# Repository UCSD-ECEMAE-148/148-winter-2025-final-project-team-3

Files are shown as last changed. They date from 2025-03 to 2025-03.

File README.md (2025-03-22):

# <div align="center">Autonomous Stock Relief</div>

### <div align="center"> MAE 148 Final Project </div>
#### <div align="center"> Team 3 Winter 2025 </div>
<p align = center>
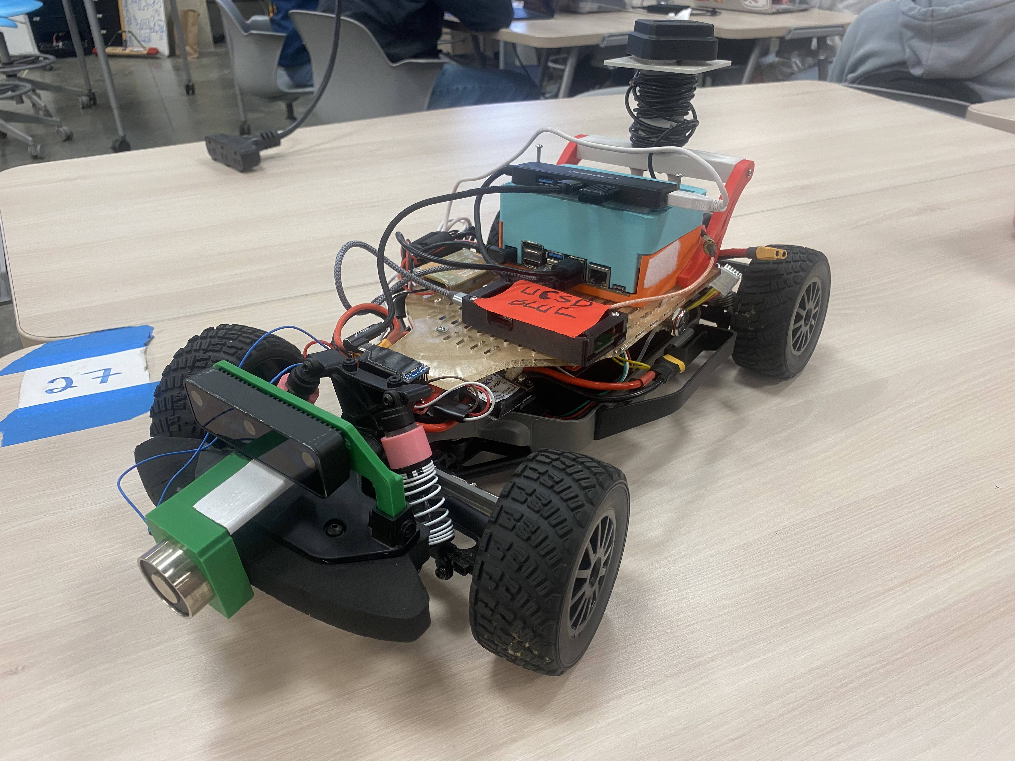
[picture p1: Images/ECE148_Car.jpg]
  
</p>

## Table of Contents
  <ol>
    <li><a href="#team-members">Team Members</a></li>
    <li><a href="#abstract">Abstract</a></li>
    <li><a href="#what-we-promised">Promises and Stretch Goals</a></li>
    <li><a href="#accomplishments">Accomplishments</a></li>
    <li><a href="#challenges">Challenges</a></li>
    <li><a href="#Potential-Improvements">Potential Improvements</a></li>
    <li><a href="#Demonstrations">Demonstrations</a></li>
    <li><a href="#Robot-Design">Robot Design</a></li>
      <ul>
        <li><a href="#Mechanical-Designs">Mechanical Designs</a></li>
        <li><a href="#Electrical-System-Diagram">Electrical System Diagram</a></li>
      </ul>
  </ol>
<hr>

## Team Members
Anton John Del Mar - ECE ML & Controls - Class of 2025

Tigran Grigoryan - MAE Controls & Robotics - Class of 2027

Kanishk Mehta - MAE Aerospace - Class of 2026

Juan Sanchez - MAE Aerospace Flight Dynamics and Control- Class of 2026
<hr>

## Abstract
The goal of our project was to create a bot that would be able to navigate between different warehouses and transport supply from overflowing warehouses to one's with less stock. To navigate between the warehouses the idea was the employ GNSS and once inside the warehouse, the bot would utilize a model running on the OAK-D Lite in order to identify boxes and pick them up with a grabbing mechanism in order to transport.
<hr>

## Promises and Stretch Goals
Promised
* Integrate GNSS, OAK-D model, and Grabber Mechanism into the ROS2 system.

Stretch Goals
* Create a "A*" algorithm in order to find the shortest distance between two warehouses and take that route.
* Integrate lidar into ROS2 system in an effort for obstacle avoidance, following a global path until reaching an obstacle and using lidar to follow a local path avoiding the obstacle and getting back onto the global path.
<hr>

## Accomplishments
- Created and integrated custom electromagnet grabber mechanism.
- Developed April Tag detection algorithm for autonomous loading of supplies.
  - Integrated our own custom PID control to self-align towards boxes with April Tags.
- Created custom GPS algorithm for autonomous navigation to warehouse points.
  - Also used custom PID control along with cross track error algorithm to stay on path.
  - Used .csv files and parsed them for GPS coordinates
<hr>

## Challenges
- Our electronics mount broke during the race, causing us to have to redesign a base and reintegrate our electronics.
- We initially made our own electromagnet, however could not integrate it with the relay circuit, causing us to have to use a store bought one.
- The first camera mount we created was too high and since it was adujustable the angle could change and require us to recallibrate our April Tag detection. We thus created a new short, fixed camera mount that also could hold our electromagnet.
- It took one week to debug and get our GPS to work. We tried two different repositories for the PointOneNav, tried different Docker containers, tried uninstalling and reinstalling the fusion-engine-driver, we tried other GPS modules, we even tried to use the Ublox, all to no avail. After one week of trieless debugging and suffering, it turns out it really was just our module. Our module simply did not work with the fusion-engine-driver in ROS2, but our TA Winston had a module that did and he let us use his.
- A lot of restless coding, debugging, and testing, trying to integrate our autonomous system fully in ROS2. 
- Issues with our Docker container caused us to lose some code and have to rewrite it.
- Jetson SD card was corrupted the day before our final presentation, and we could not save our Docker conatiner. Causing us to have to reflash our SD card, reinstall and setup everything such as pulling and setting up the Docker image, and also having to rewrite a lot of missing code.
- Created our own topic and message interface for our GPS and April Tag nodes, but then our VESC stopped working, preventing us from testing the interface.

<hr>

## Potential Improvements
- Create a new camera mount such that the camera is a bit farther back, because since the camera was in the front it could not see the April Tag if it was too close.
- Design a different electromagnet grabber, our design required the boxes to be on a little pallet. Maybe have the electromagnet pick up boxes from above like a crane.
- Integrate a better circuit design using perf boards or even a PCB rather than just connecting everything with wires and electrical tape. 
- Complete testing the custom topic and interface to fully integrate the April Tag and GPS nodes. 

<hr>

## Progress Videos

### Electromagnet Testing
**Description:**  
Demonstration of our custom electromagnet, and later the Arduino relay circuit with a store bought electromagnet communicating via SPI to the Jetson.

Custom Electromagnet (https://youtube.com/shorts/Nj_8vAmQDf4?feature=share)
Jetson and Arduino Talking (https://youtube.com/shorts/6ehe19gdT4E?feature=share)

### April Tag Testing
**Description:**  
Initial April Tag detection algorithm, April Tag detection without PID tuning, and finally April Tag detection with PID tuning as well as a POV shot of what the robot sees during self-alignment.

Inital April Tag Detection (https://youtube.com/shorts/lWoA0QRKPfw?feature=share)
No PID (https://youtube.com/shorts/V5mrUUOpYhs?feature=share)
April Tag PID (https://youtube.com/shorts/OQ9bbp3Mwuc?feature=share)
April Tag PID POV (https://youtube.com/shorts/0pPFK0INl1c?feature=share)

### GPS Testing
**Description:**  
Initial GPS testing without PID tuning.

GPS no PID (https://youtube.com/shorts/9fqmz0wuvG4?feature=share)

<hr>

## Final Demonstrations

### April Tag Detection and GPS Navigation
**Description:**  
Sucessfull autonomous loading of supply with April Tag Detection using PID tuning. Succesfull autonomous navigation to a warehouse point 'A' using GPS and PID tuning as well.

Final April Tag (https://youtube.com/shorts/S16Okz2q1UY?feature=share)
Final GPS (https://youtube.com/shorts/vWnwtKYyrfo?feature=share)

<hr>

## Robot Design

### Mechanical Designs
| Part | CAD Model |
|---|---|
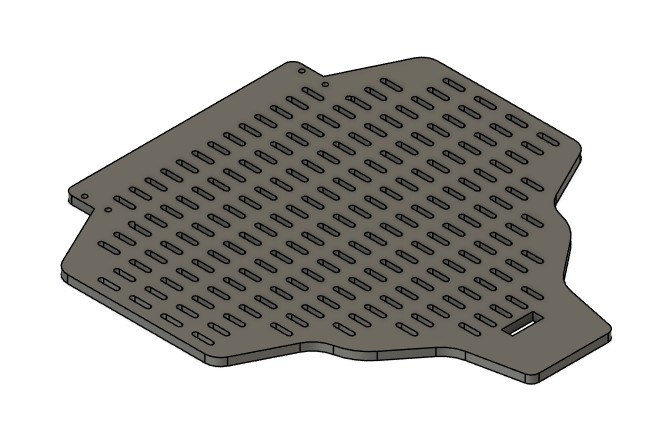
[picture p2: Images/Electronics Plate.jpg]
Electronics Plate
| Electronics Mounting Plate | <br>[🔗 CAD File](CAD%20Files/New%20Chassis/Electronics%20plate%20v13.f3d) |
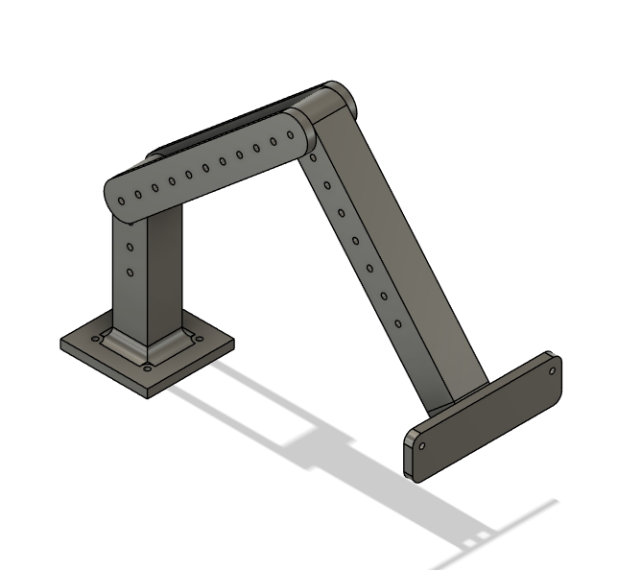
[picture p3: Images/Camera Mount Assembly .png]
Camera Mount
| Camera Mount | <br>[🔗 CAD File](CAD%20Files/New%20Chassis/Camera%20Mount/Camera%20Mount%20assembly%20v5.f3z) |
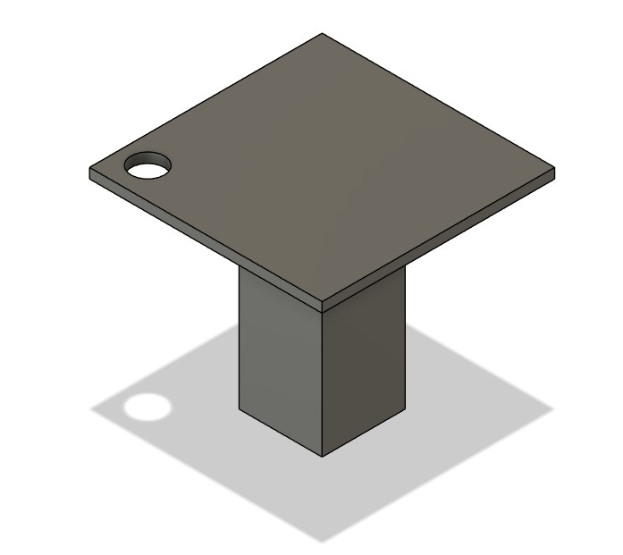
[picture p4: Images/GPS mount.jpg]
GPS Mount
| GPS Mount | <br>[🔗 CAD File](CAD%20Files/New%20Chassis/Gps%20mount%20v2.f3d) |
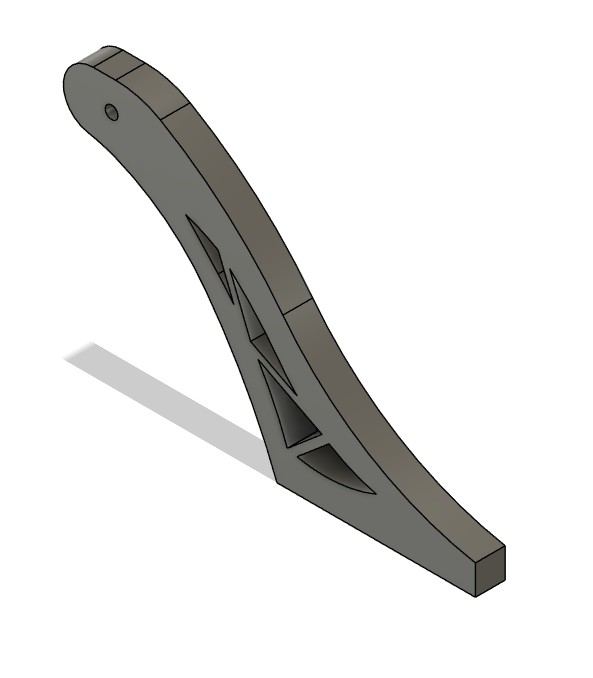
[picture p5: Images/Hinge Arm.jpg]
Hinge Arm
| Hinge Arm | <br>[🔗 CAD File](CAD%20Files/New%20Chassis/Hinge%20arm%20v8.f3d) |
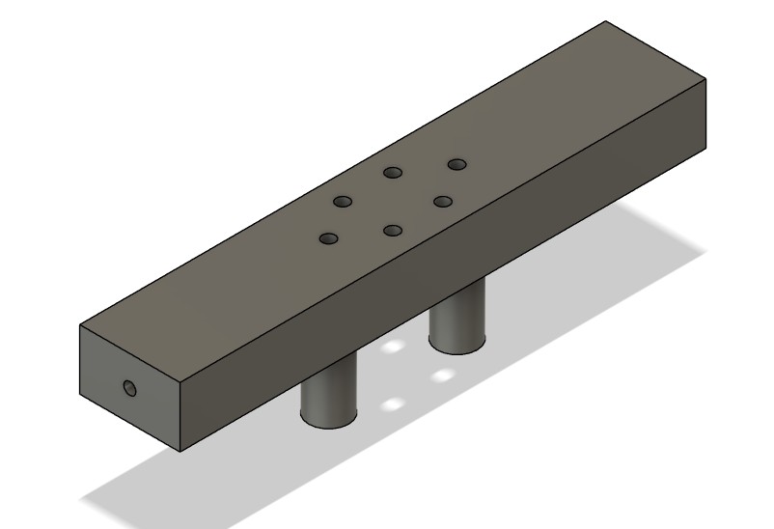
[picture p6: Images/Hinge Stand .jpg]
Hinge and GPS stand
| Hinge and GPS stand | <br>[🔗 CAD File](CAD%20Files/New%20Chassis/GPS+hinge%20stand%20v8.f3d) |
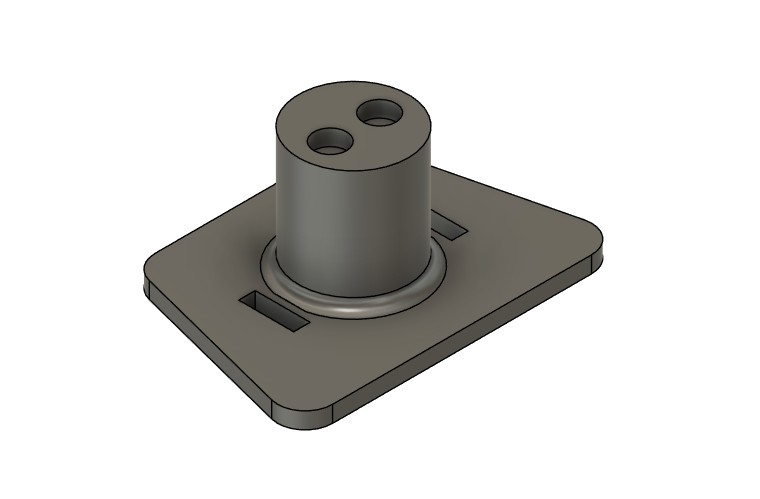
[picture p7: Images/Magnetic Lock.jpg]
Magnetic Lock
| Magnetic Lock | <br>[🔗 CAD File](CAD%20Files/New%20Chassis/Magnetic%20Lock%20v7.f3d) |
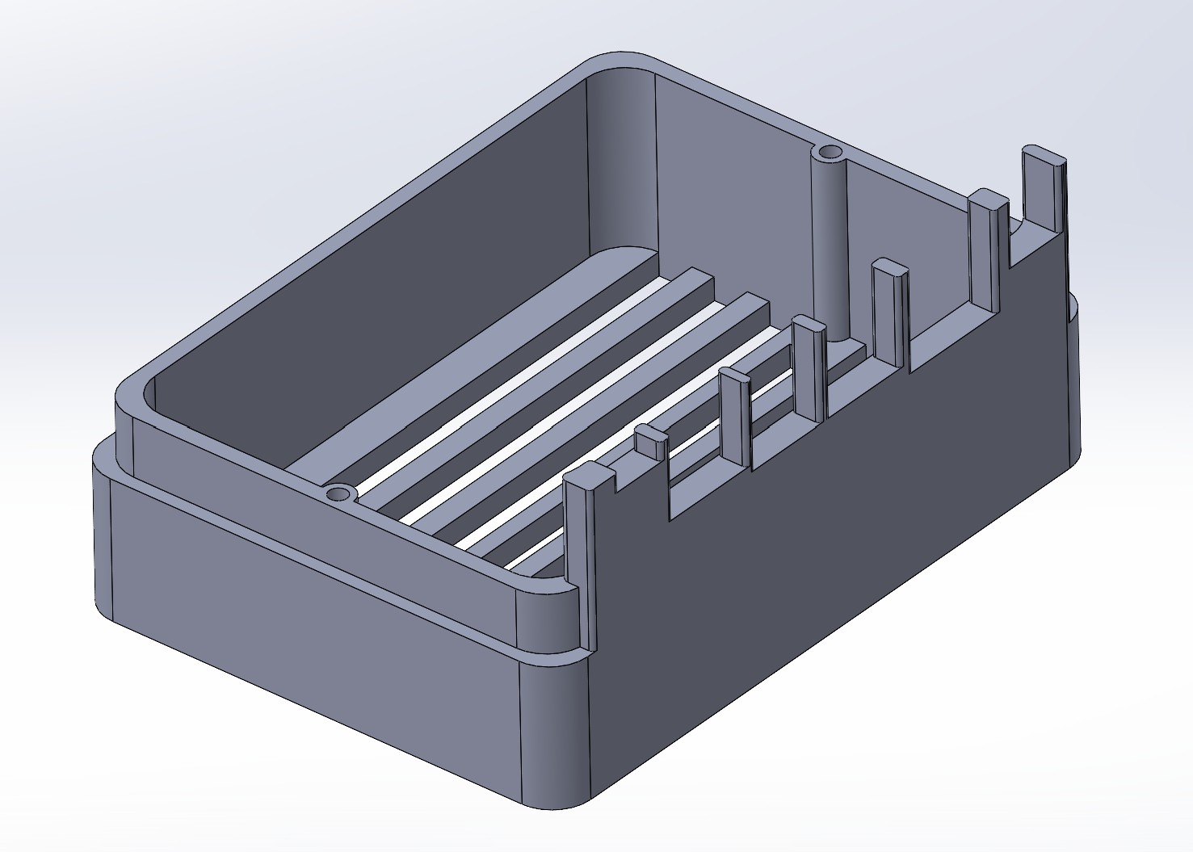
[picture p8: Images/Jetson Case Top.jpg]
Jetson Case
| Jetson Case Top | <br>[🔗 CAD File](CAD%20Files/New%20Chassis/Jetson%20Top%20V1.SLDPRT) |
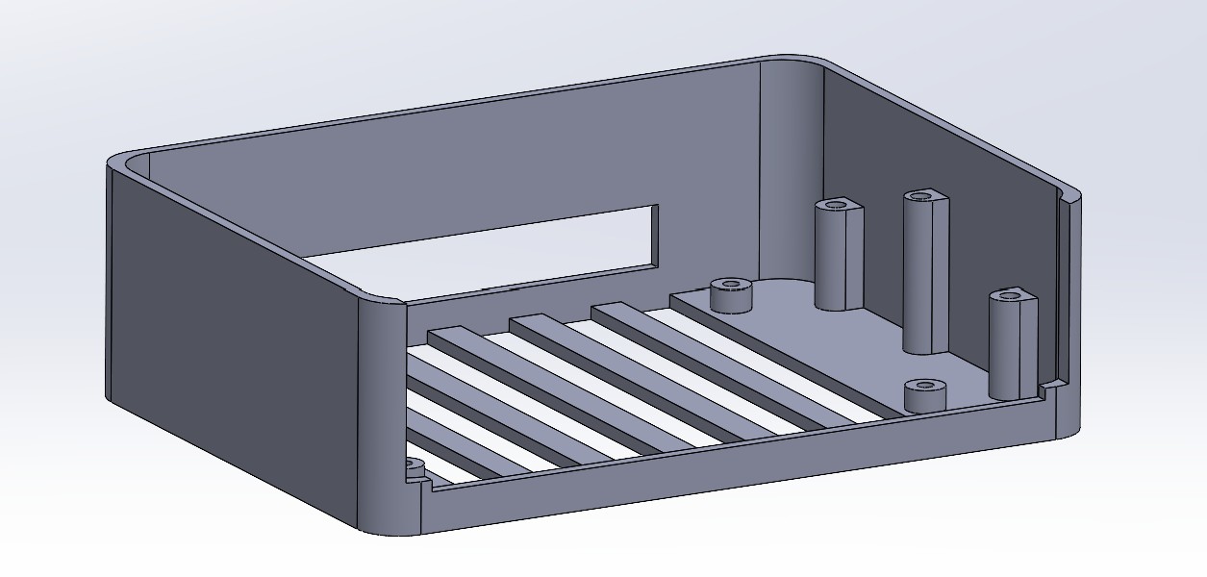
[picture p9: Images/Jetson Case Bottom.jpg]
Jetson Case
| Jetson Case Bottom | <br>[🔗 CAD File](CAD%20Files/New%20Chassis/Jetson%20Bottom%20V1.SLDPRT) |
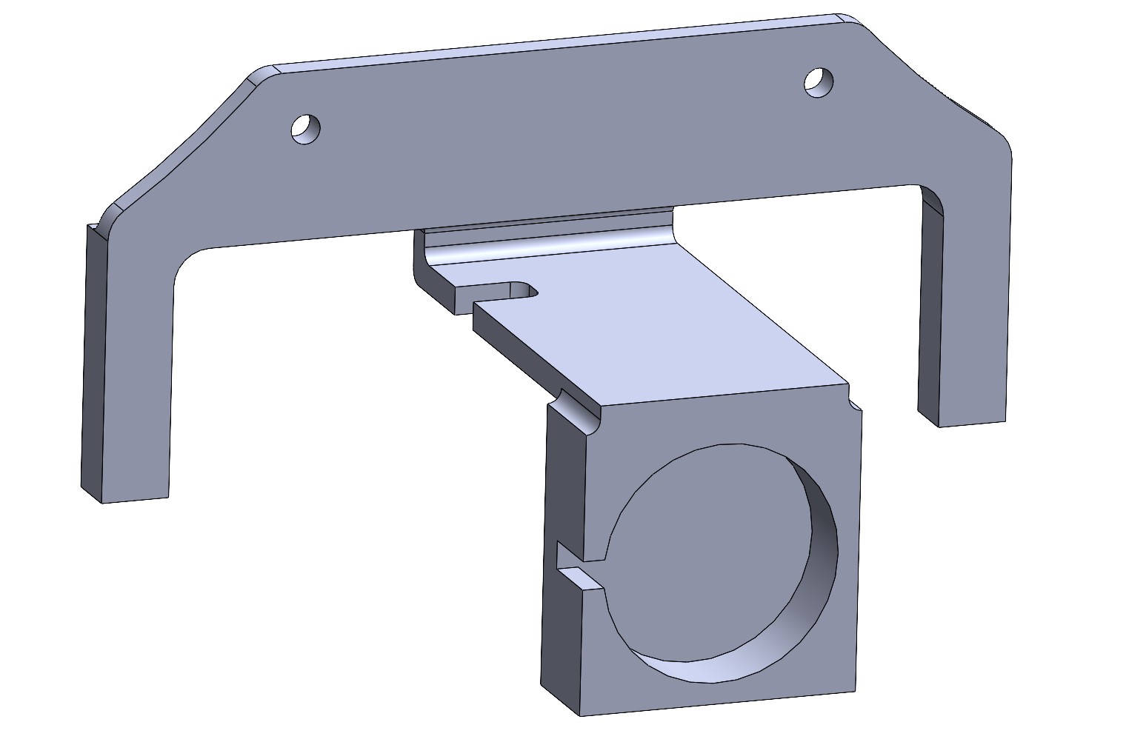
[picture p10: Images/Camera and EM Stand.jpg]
| Camera and ElectroMagnet Stand | <br>[🔗 CAD File](CAD%20Files/New%20Chassis/Camera%20and%20EM%20Stand.SLDPRT) |
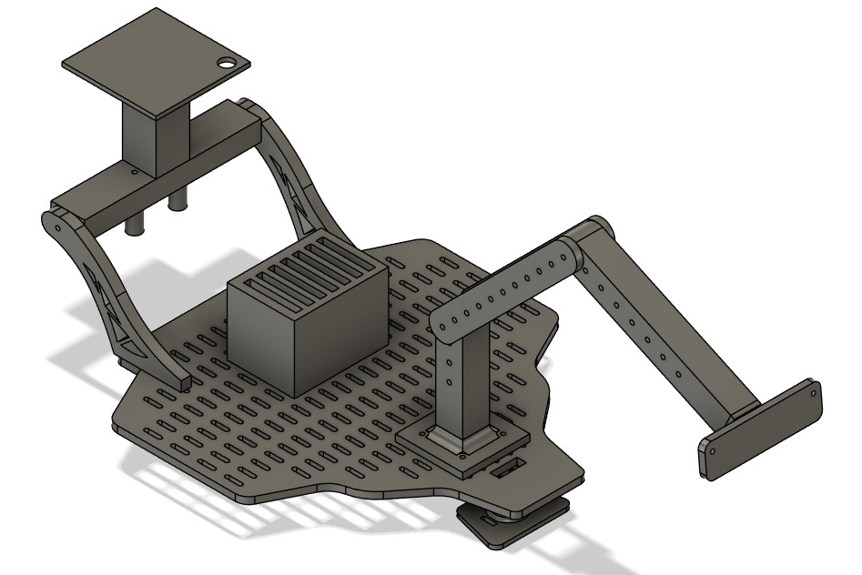
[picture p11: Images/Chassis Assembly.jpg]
New Chassis Assembly
| New Chassis Assembly | <br>[🔗 CAD File](CAD%20Files/New%20Chassis/Assemply%20v7.f3z) |

<hr>

### Electrical System Diagram
| Comprehensive Wiring Diagram |
|------|
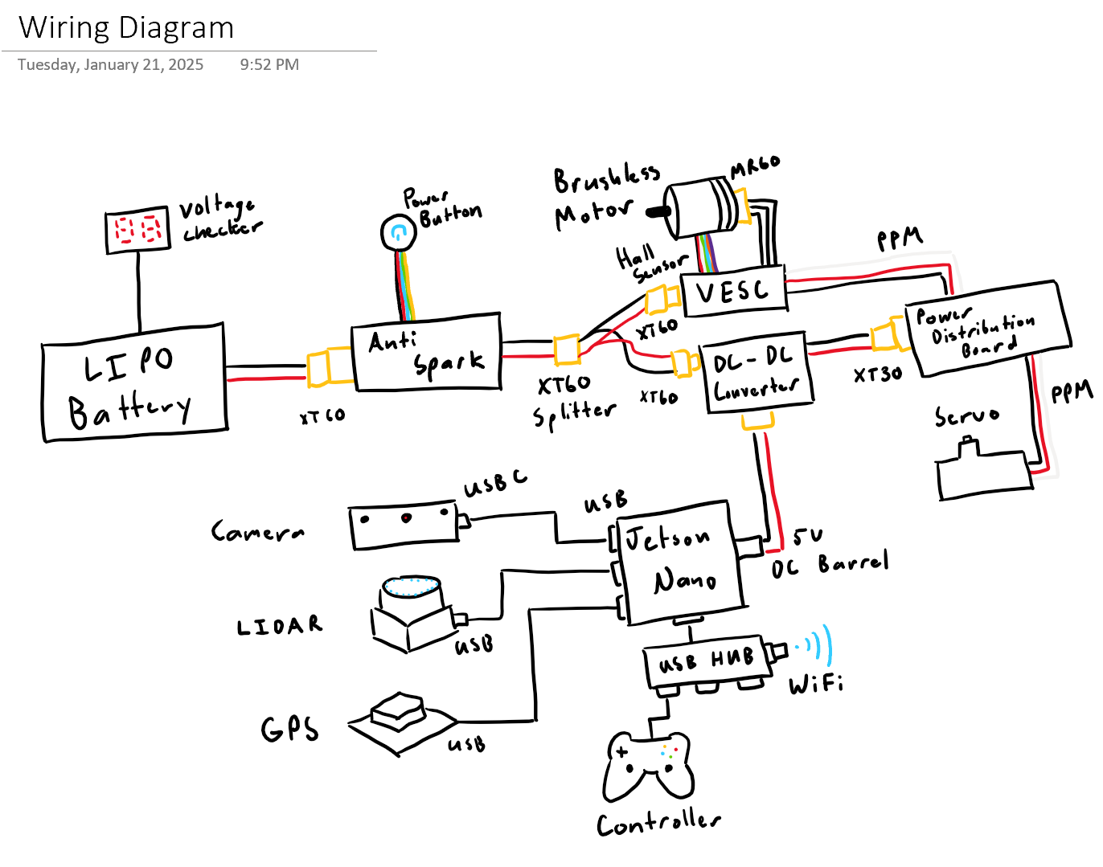
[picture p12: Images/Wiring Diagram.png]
Comprehensive Wiring Diagram
|  |

<hr>

## Software Design 
### Overview 
Our project was completed using ROS2 through the djnighti/ucsd_robocar container, also utilizing libraries such as DepthAI AprilTag and pymap3d. With the use of ROS2 we were able to have free reign over our code allowing for full control and custom development of our autonomous system.

### Code Explanations 
april_tag_detector.py, car_control.py, PID.py
- april_tag_detector.py: We succesfully utilized ROS2 and DepthAI's April Tag library in order to allow our OAK-D camera to detect April Tags. We calculate how far the April Tag is and how off-center it is as well to determine how much to turn and drive.
  - Created a custom circuit that used an Arduino Pro Micro to control a relay to turn on and off our electromagnet, then used Python's serial library to allow our Jetson to interface with the circuit and turn on the electromagnet when needed. 
- car_control.py: we use the /drive topic with ackermann_msgs/msg/AckermannDriveStamped interface message type to control speed and steering angle of the bot.
- PID.py: With initial testing we found our robot would turn too much in proportion to the error. We created a PID class to help fine tune our robots self-alignment with April Tags.

gps_navigation.py, coordinates.csv
- gps_navigation.py: We succesfully utilized the PointOneNav GNSS in ROS2 order to get global positions and navigate between warehouses. Using Python's pymap3d library we can convert global coordinates into relative coordinates. For navigation we use pandas library to read a .csv file tellings us the origin and the coordinate of a warehouse, then simply use y = mx + b to determine the path by creating a straight line to the warehouse. We can now use cross track error and the determinant of two vectors to see how we deviate from the line and see which side we are on, and then use our PID class to realign ourselves onto the path.
- coordinates.csv: Holds the coordinates for the warehouse and origin.

final_project.launch.py, gps_april_msgs
- final_project.launch.py: Created a launch file that would launch our april_tag_detector.py and gps_navigation.py nodes, as well as the ucsd_robocar_nav2_pkg all_nodes.launch.py that would launch the vesc node.
- gps_april_msgs: Created a custom message interface called gps_april_msgs/msg/GpsApril along with a new topic named /GpsApril to allow the April Tag and GPS nodes to talk to eachother. This interface contained important information like if the robot was in approach mode or origin mode to tell it if it needs to drive to a warehouse or return to an origin, the warehouse name it needs to go to, as well as GPS mode and April Tag mode to well it when to run April Tag detection or GPS navigation.

### Implementation
If you wish to implement our code into your own project it is really simple! You can use the same container as you did for the OpenCV laps as we used the djnighti image with ROS2 for this one. All of our code was completed inside the ucsd_robocar_nav2_pkg, so simply add the code into this package. Make sure you add the executables in setup.py and if you rename them make sure to modify the launch file as well. If you want to create your own topic or interface you have to create a new package in ucsd_robocar_hub2, where all the packages are stored, in this case you can simply copy our folder as it has set up all the Cmake files already, you simply would just have to change the names to whatever you want. That is about it, have fun and goodluck!

<hr>

## Gantt Chart
<p align = center>
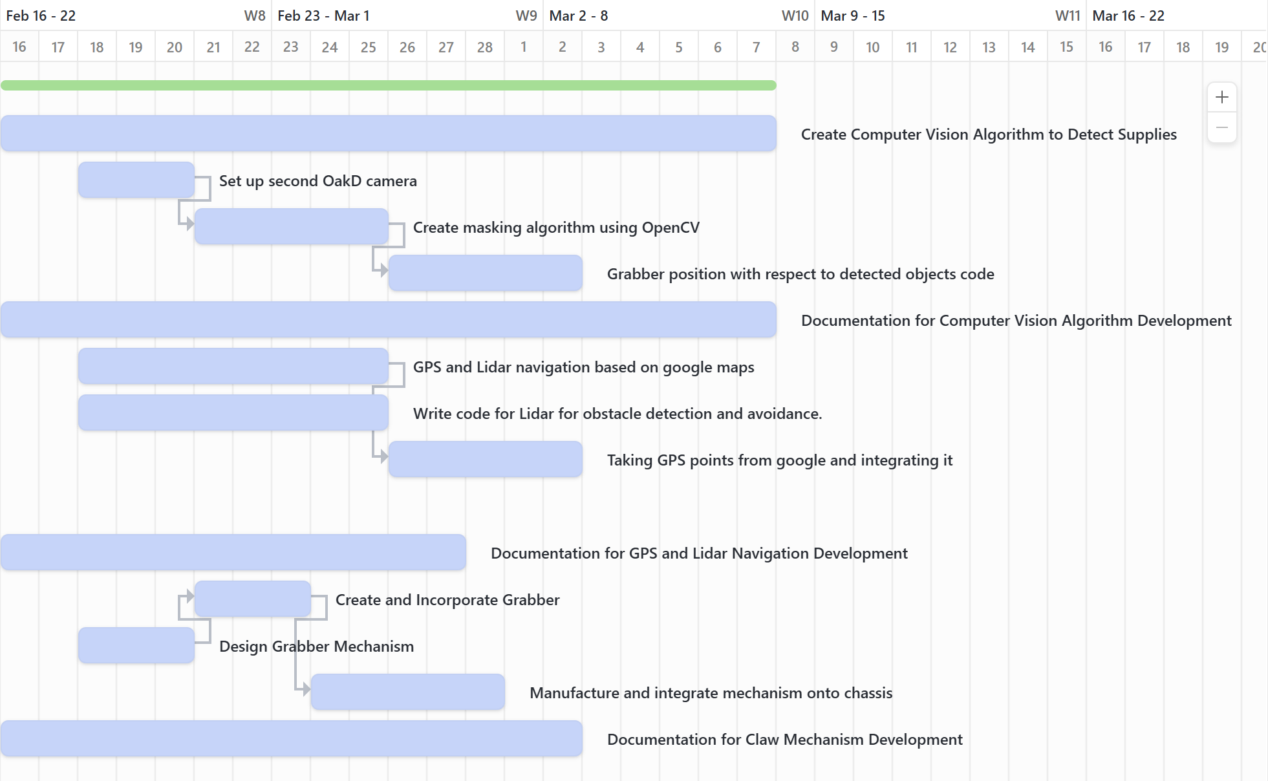
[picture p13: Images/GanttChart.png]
  
</p>

<hr>

## Course Deliverables
Here are all the team assignments we had to complete for the course.
- [Autonomous Laps](https://youtube.com/shorts/bM4KuNR4FdE?si=LPRqq_h8zV2o7q9d)
- [GPS Laps](https://youtu.be/LaXMkxYxspk)
- [OpenCV Laps](https://youtu.be/_cmjnNDHkDQ?si=lZVS0dAk0vt-fLF-)
- [Progress Update Slides](https://docs.google.com/presentation/d/1vnkvjQhTCcCYGIWP700G1c7TLgcMM7nZI48wmxLYrfw/edit?usp=sharing)
- [Final Presentation Slides](https://docs.google.com/presentation/d/1t6mhh3AGAhgKwmr5gQEw1CEoPPurwSvcvcnYaqPXGoU/edit?usp=sharing)

<hr>

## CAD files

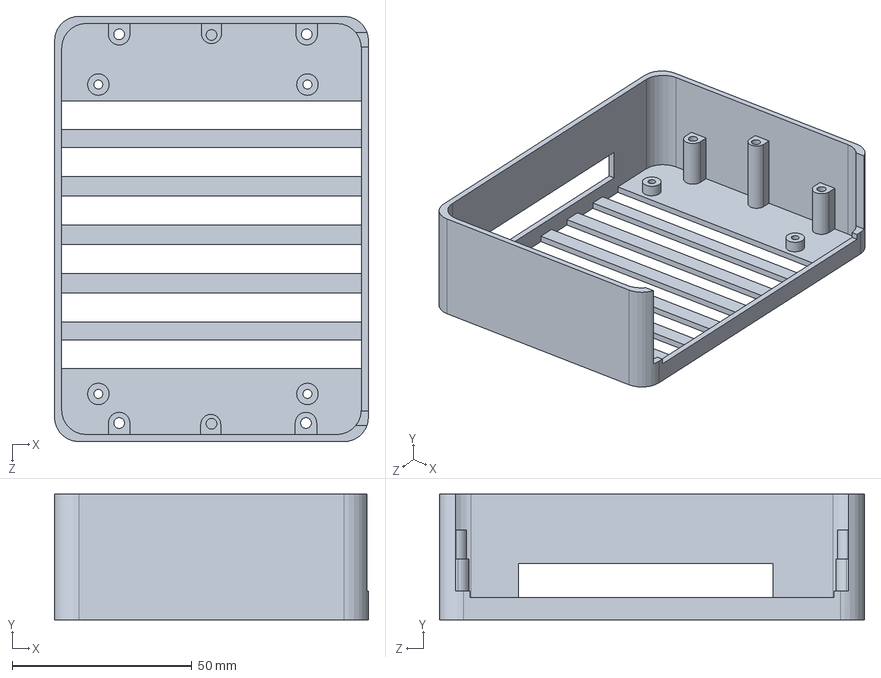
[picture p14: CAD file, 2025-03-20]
CAD Files/New Chassis/Jetson Bottom V1.SLDPRT
87.4 x 35.0 x 118.4 mm

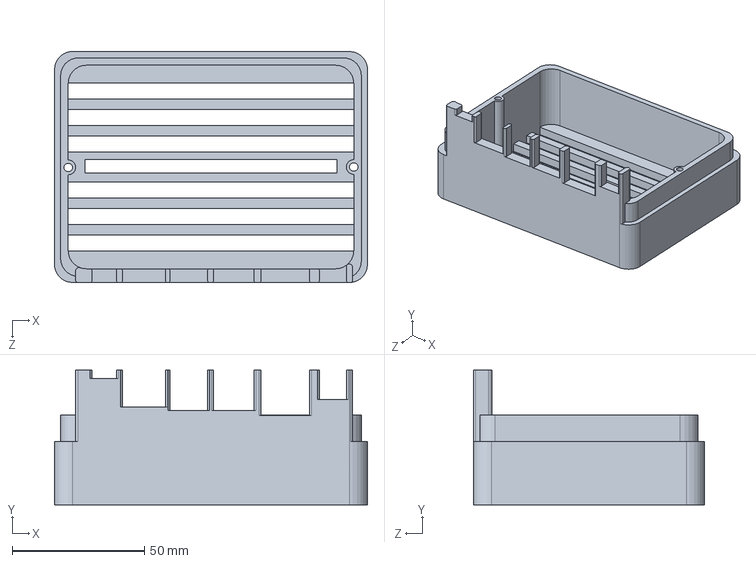
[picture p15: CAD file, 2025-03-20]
CAD Files/New Chassis/Jetson Top V1.SLDPRT
118.4 x 51.0 x 87.4 mm

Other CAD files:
CAD Files/New Chassis/Assemply v7.f3z
CAD Files/New Chassis/Camera Mount/Camera Mount assembly v5.f3z
CAD Files/New Chassis/Camera Mount/Camera arm 1 v5.f3d
CAD Files/New Chassis/Camera Mount/Camera arm 2 v4.f3d
CAD Files/New Chassis/Camera Mount/Camera mount negative v2.f3d
CAD Files/New Chassis/Camera Mount/Camera mount v2.f3d
CAD Files/New Chassis/Camera Mount/camera stand v4.f3d
CAD Files/New Chassis/Electronics plate v13.f3d
CAD Files/New Chassis/GPS+hinge stand v8.f3d
CAD Files/New Chassis/Gps mount v2.f3d
CAD Files/New Chassis/Hinge arm v8.f3d
CAD Files/New Chassis/Magnetic Lock v7.f3d
CAD Files/Old Chassis/Old_Camera Mount v1.f3d
CAD Files/Old Chassis/Old_Electronics plate v1.f3d
CAD Files/Old Chassis/Old_gps mount v2.f3d

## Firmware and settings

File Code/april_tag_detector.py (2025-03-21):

import cv2
import depthai as dai
import numpy as np
import serial
import time
from numpy import interp

import rclpy
from rclpy.node import Node

from ucsd_robocar_nav2_pkg.car_control import moveCar
from ucsd_robocar_nav2_pkg.PID import controlPID

from gps_april_msgs.msg import GpsApril


class AprilTag(Node):
	def __init__(self):
		super().__init__("april_tag_node"); 
		self.declare_parameter('detect', False); 
		self.declare_parameter('visualize', False); 
		
		self.checkDetect = self.get_parameter('detect').value; 
		self.checkVisualize = self.get_parameter('detect').value; 
		
		self.talkPublisher = self.create_publisher(GpsApril, '/talkGpsApril', 10); 
		self.talkSubscriber = self.create_subscription(
			GpsApril,
			'/talkGpsApril',
			self.GpsAprilChecker,
			10
		); 
		self.talkSubscriber; 
		
		self.theCar = moveCar(); 
		self.theCar.stopCar(); 
		self.PID = controlPID(Kp = 0.4, Ki = 0, Kd = 0.15, theError = 0.0); 
		
		self.targetID = 0; 
		self.theThreshold = 12000; # Box is about 6in away
		
		self.theSerial = serial.Serial(port = "/dev/ttyACM0", baudrate = 9600); 
		
		self.aprilMode = False; 
	
		if self.checkDetect: 
			self.aprilDetection(); 
			
	def GpsAprilChecker(self, theMessage):
		self.get_logger().info("Message Received: " + str(theMessage)); 
		self.aprilMode = theMessage.april_mode; 
	
	
	def aprilDetection(self): 
		thePipeline = dai.Pipeline(); 
		cameraRGB = thePipeline.create(dai.node.ColorCamera); 
		# print(str(cameraRGB.getResolution())); 
		cameraRGB.setPreviewSize(960, 540); # Our camera is 1080, so 1920 x 1080 frame size
		cameraRGB.setInterleaved(False); 
		cameraRGB.setFps(30); 
		
		aprilTag = thePipeline.create(dai.node.AprilTag); 
		cameraRGB.video.link(aprilTag.inputImage); 
		
		xOutDetections = thePipeline.create(dai.node.XLinkOut); 
		xOutDetections.setStreamName("Detection Stream"); 
		aprilTag.out.link(xOutDetections.input); 
		
		xOutVideo = thePipeline.create(dai.node.XLinkOut); 
		xOutVideo.setStreamName("Video Stream"); 
		cameraRGB.preview.link(xOutVideo.input); 
			
		with dai.Device(thePipeline) as theDevice:
			aprilQueue = theDevice.getOutputQueue(name = "Detection Stream", maxSize = 4, blocking = False);
			videoQueue = theDevice.getOutputQueue(name = "Video Stream", maxSize = 4, blocking = False);
		
			while True: 
				if self.aprilMode:
					try:
						theDetections = aprilQueue.get(); 
					except RuntimeError as theError:
						self.get_logger().info("Camera Error: " + str(theError));
						time.sleep(4); 
						continue; 
							
					theFrame = videoQueue.get().getCvFrame(); 
					
					if self.checkVisualize: 
						cv2.line(theFrame, (480, 540), (480, 0), (0, 255, 0), 2); 
				
					if theDetections is not None: 
						for aDetection in theDetections.aprilTags:
							tagID = aDetection.id; 
							# self.get_logger().info("Tag ID: " + str(tagID));  
							# Map coordinate to our preview size using interpolate
							xBR = aDetection.bottomRight.x; 
							xBR = int(np.interp(xBR, [0, 1920], [0, 960])); 
							yBR = aDetection.bottomRight.y; 
							yBR = int(np.interp(yBR, [0, 1080], [0, 540])); 
							# self.get_logger().info("Bottom Right Coordinate: " + str(xBR) + ", " + str(yBR)); 
							
							xTL = aDetection.topLeft.x; 
							xTL = int(np.interp(xTL, [0, 1920], [0, 960])); 
							yTL = aDetection.topLeft.y; 
							yTL = int(np.interp(yTL, [0, 1080], [0, 540])); 
							# self.get_logger().info("Top Left Coordinate: " + str(xTL) + ", " + str(yTL)); 
							
							xMiddle = int(xBR - ((xBR - xTL)/2)); 
							yMiddle = int(yTL - ((yTL - yBR)/2)); 
								
							theError = xMiddle - 480; 
							self.get_logger().info("Error: " + str(theError)); 
							
							theHeight = int(yTL - yBR); 
							theWidth = int(xBR - xTL); 
							
							theArea = np.abs(theHeight * theWidth); 
							self.get_logger().info("Area: " + str(theArea)); 
						
							if tagID == self.targetID:
								if theArea < self.theThreshold:
									theAngle = self.PID.computePID(theError); 
									theAngle = np.interp(theAngle, [-180, 180], [-0.5, 0.5]); 
									self.get_logger().info("Angle: " + str(theAngle)); 
									self.theCar.driveCar(0.3, theAngle); 
									time.sleep(1); 
									
								if theArea > self.theThreshold:
									self.theSerial.write("on".encode('Ascii')); 
									time.sleep(1); 
								
									theAngle = self.PID.computePID(theError); 
									theAngle = np.interp(theAngle, [-180, 180], [-0.5, 0.5]); 
									self.get_logger().info("Angle: " + str(theAngle)); 
									self.theCar.driveCar(0.4, theAngle); 
									time.sleep(2); 
									self.theCar.driveCar(-0.3, 0.0); 
									
									self.theCar.turnAround(); 
									self.theCar.driveCar(0.5, 0.0); 
									self.theSerial.write("off".encode('Ascii')); 
									self.theSerial.close(); 
									time.sleep(2); 
									self.theCar.driveCar(-0.5, 0.0); 
								
							if self.checkVisualize:
								cv2.rectangle(theFrame, (xTL, yTL), (xBR, yBR), (255, 0, 0), 2); 
								cv2.line(theFrame, (xMiddle, yMiddle), (480, yMiddle), (0, 0, 255), 2); 
								cv2.putText(theFrame, str(tagID), (xMiddle, yMiddle), cv2.FONT_HERSHEY_SIMPLEX, 1, (255, 255, 255), 2, cv2.LINE_AA); 
							 				
					 
					if self.checkVisualize:
						cv2.imshow("April Tag", theFrame); 
					
					if cv2.waitKey(1) and 0xFF == ord('q'):
						break; 
						
				cv2.destroyAllWindows(); 
				 
				 

def main(args = None): 
	rclpy.init(args = args); 
	
	nodeAprilTag = AprilTag(); 
	
	rclpy.spin(nodeAprilTag); 
	
	rclpy.shutdown(); 
	
	
	
if __name__ == '__main__':
	main(); 

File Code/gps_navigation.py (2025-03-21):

import os
import pandas as pd
import numpy as np
import pymap3d as pmap

import rclpy
from rclpy.node import Node
from rclpy.qos import QoSProfile, ReliabilityPolicy, DurabilityPolicy

from sensor_msgs.msg import NavSatFix
from ucsd_robocar_nav2_pkg.car_control import moveCar
from ucsd_robocar_nav2_pkg.PID import controlPID

from gps_april_msgs.msg import GpsApril


class gpsNavigationNode(Node):
	def __init__(self):
		super().__init__("gps_navigation_node"); 
		# self.get_logger().info("GPS Node Activated!");

		# self.get_logger().info(str(os.getcwd()));
		dataFrame = pd.read_csv("src/ucsd_robocar_hub2/ucsd_robocar_nav2_pkg/ucsd_robocar_nav2_pkg/coordinates.csv");

		# theData = self.parseData(dataFrame);

		# self.get_logger().info(str(theData['A']));

		theQoS = QoSProfile(depth = 10, reliability=ReliabilityPolicy.BEST_EFFORT, durability=DurabilityPolicy.VOLATILE);
		self.theSubscriber = self.create_subscription(
			NavSatFix,
			'/fix',
			self.getCoordinate,
			theQoS
		); 
		self.theSubscriber; 
		
		self.talkPublisher = self.create_publisher(GpsApril, '/talkGpsApril', 10);
		self.talkSubscriber = self.create_subscription(
			GpsApril,
			'/talkGpsApril',
			self.GpsAprilChecker,
			10
		); 
		self.talkSubscriber; 


		self.theLat0 = 32.88115036131583; 
		self.theLon0 = -117.23339932288448; 
		self.theAlt0 = 74.33511395566165; 

		csvInfo = self.parseData(dataFrame); 
		self.theTarget = csvInfo['A']; 
		self.theTargetE = self.theTarget[0]; 
		self.theTargetN = self.theTarget[1]; 
		
		# Initialize interface, we start with GPS
		theMessage = GpsApril(); 
		theMessage.target_name = "A"; 
		theMessage.approach_target = True; 
		theMessage.gps_mode = True; 
		self.talkPublisher.publish(theMessage); 
		
		self.PID = controlPID(Kp = 0.2, Ki = 0, Kd = 0.12, theError = 0.0); 
		self.theCar = moveCar(); 
		self.theCar.stopCar(); 
		
		self.approachTarget = False; 
		self.returnOrigin = False; 
		self.targetName = ""; 
		self.gpsMode = False; 
		
		
	def GpsAprilChecker(self, theMessage):
		self.get_logger().info("Message Received: " + str(theMessage)); 
		self.approachTarget = theMessage.approach_target; 
		self.returnOrigin = theMessage.return_origin; 
		self.targetName = theMessage.target_name; 
		self.gpsMode = theMessage.gps_mode; 
		
		
	def euclideanDistance(self, theE, theN, theU):
		theDistance = np.sqrt((self.theTargetE - theE)**2 + (self.theTargetN - theN)**2);
		return theDistance; 


	def lineSide(self, theE, theN): # Which side of the line we are on using the determinant of two vectors
		# Determine the side of the line we are on using sign function
		# det = (x2 - x1)*(p_y - y1) - (y2 - y1)*(p_x - x1);
		# Origin = (x1, y1), Target = (x2, y2), Point = (p_x, p_y);
		# We want to check if the point is on the left or right of the line made by origin and target
		# If the determinant is greater than 0 it is left, less than it is right, exactly 0 is on line
		x1 = 0; y1 = 0; x2 = self.theTargetE; y2 = self.theTargetN; 
		p_x = theE; p_y = theN; 
		theDeterminant = (x2 - x1)*(p_y - y1) - (y2 - y1)*(p_x - x1); 
		return np.sign(theDeterminant); 
		
		
	def crossTrackError(self, theE, theN): # How far a point is from a line
		# Distance from line = Ax + By + C / sqrt(A**2 + B**2);
		# Ax + By + C = 0, y = mx + b, mx - y + b = 0, C = b, B = -1, A = m
		A = self.theTargetN/self.theTargetE; B = -1; C = 0; 
		x = theE; y = theN; 
		CTE = (np.abs(A*x + B*y + C) / np.sqrt(A**2 + B**2)); 
		return CTE; 
		
		
	def driveTarget(self, theE, theN, theU):
		# self.get_logger().info(str(self.gpsMode)); 
		if self.gpsMode and self.approachTarget:
			theDistance = self.euclideanDistance(theE, theN, theU); 
			self.get_logger().info("Euclidean Distance: " + str(theDistance)); 

			theCTE = self.crossTrackError(theE, theN); # Distance from line
			theCTE = theCTE*self.lineSide(theE, theN); # Side of line
			self.get_logger().info("Cross Track Error: " + str(theCTE)); 

			if theDistance < 0.7:
				self.theCar.stopCar(); 
				theMessage = GpsApril(); 
				theMessage.approach_target = False; 
				theMessage.gps_mode = False; 
				theMessage.april_mode = True; 
				self.talkPublisher.publish(theMessage); 

			else:
				theAngle = self.PID.computePID(theCTE); 
				self.get_logger().info("Angle: " + str(theAngle)); 
				self.theCar.continuousDrive(0.3, theAngle); 


	def getCoordinate(self, theMessage):
		NS = theMessage.latitude; # (+) = North, (-) = South
		EW = theMessage.longitude; # (+) = East, (-) = West
		ALT = theMessage.altitude; 
		self.get_logger().info(f"East: {EW}, North: {NS},  Alt: {ALT}"); 

		# Convert to ENU
		theE, theN, theU = pmap.geodetic2enu(NS, EW, ALT, self.theLat0, self.theLon0, self.theAlt0); 

		self.get_logger().info(f"E: {theE}, N: {theN}, U: {theU}"); 
		self.driveTarget(theE, theN, theU); 


	def parseData(self, dataFrame):
		dataDictionary = {}; 
		for anIndex, aRow in dataFrame.iterrows():
			# self.get_logger().info(f"Index: {anIndex}");
			# self.get_logger().info(f"Warehouse: {aRow['warehouse']}, East: {aRow['east']}, North: {aRow['north']}");
			dataDictionary.update({aRow['warehouse']: (aRow['east'], aRow['north'], aRow['up'])}); 
		return dataDictionary; 


def main(args = None):
	rclpy.init(args = args); 

	gpsNode = gpsNavigationNode(); 

	rclpy.spin(gpsNode); 

	gpsNode.destroy_node(); 
	rclpy.shutdown(); 


if __name__ == '__main__':
	main(); 

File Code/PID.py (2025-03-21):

import time


class controlPID():  
	def __init__(self, Kp, Ki, Kd, theError = 0): 
		self.previousError = theError; 
		self.previousTime = time.time(); 
		self.integralTerm = 0;  
		
		self.Kp = Kp; 
		self.Ki = Ki; 
		self.Kd = Kd; 
		
		
	def computePID(self, theError): 
		currentTime = time.time(); 
		errorDifference = theError - self.previousError; 
		timeDifference = currentTime - self.previousTime; 
		
		if timeDifference == 0: 
			timeDifference = 1; # Prevent division by 0 
		
		proportionalTerm = self.Kp * theError; 
		
		self.integralTerm += theError * timeDifference; 
		integralTerm = self.Ki *self.integralTerm; 
		
		derivativeTerm = errorDifference / timeDifference; 
		derivativeTerm = self.Kd * derivativeTerm; 
		
		PID = proportionalTerm + integralTerm + derivativeTerm; 
		
		self.previousError = theError; 
		self.previousTime = currentTime; 
		
		return PID; 

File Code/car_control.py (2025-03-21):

import numpy as np
import time
from rclpy.node import Node

from ackermann_msgs.msg import AckermannDriveStamped as ADS


class moveCar(Node): 
    def __init__(self):
    	super().__init__('move_car_node'); 
        self.thePublisher = self.create_publisher(ADS, '/drive', 10); 
        
    
    def driveCar(self, theSpeed, theAngle):
        theMessage = ADS(); 
        theMessage.drive.speed = theSpeed; 
        theMessage.drive.steering_angle = theAngle; 
        self.thePublisher.publish(theMessage); 
        time.sleep(0.5); 
        theMessage.drive.speed = 0.0; 
        self.thePublisher.publish(theMessage); 
        time.sleep(0.5); 
         
    
    def stopCar(self): 
        theMessage = ADS(); 
        theMessage.drive.speed = 0.0; 
        theMessage.drive.steering_angle = 0.0; 
        self.thePublisher.publish(theMessage); 
        time.sleep(0.5)
        
    
    def turnAround(self): 
	    self.driveCar(-0.8, 0.7); 
        self.driveCar(-0.8, 0.7); 
        self.driveCar(-0.8, 0.7); 
        time.sleep(1); 
        self.driveCar(0.8, -0.7); 
        self.driveCar(0.8, -0.7); 
        self.driveCar(0.8, -0.5); time.sleep(1); 
	    
	
    def continuousDrive(self, theSpeed, theAngle):
        theMessage = ADS(); 
        theMessage.drive.speed = theSpeed; 
        theMessage.drive.steering_angle = theAngle; 
        self.thePublisher.publish(theMessage);	    
        

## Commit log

2025-03-16 Create Old Chassis
    Old chassis files
2025-03-16 Delete CAD Files directory
    Remaking the thing
2025-03-16 Create New chassis files
2025-03-16 Delete CAD Files/Old Chassis/Old files
    Dont need this anymore
2025-03-20 Create camera files
2025-03-21 Final Project Code !
    [coordinates.csv]
